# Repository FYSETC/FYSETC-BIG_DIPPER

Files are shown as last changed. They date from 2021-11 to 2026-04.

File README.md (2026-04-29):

# Big dipper

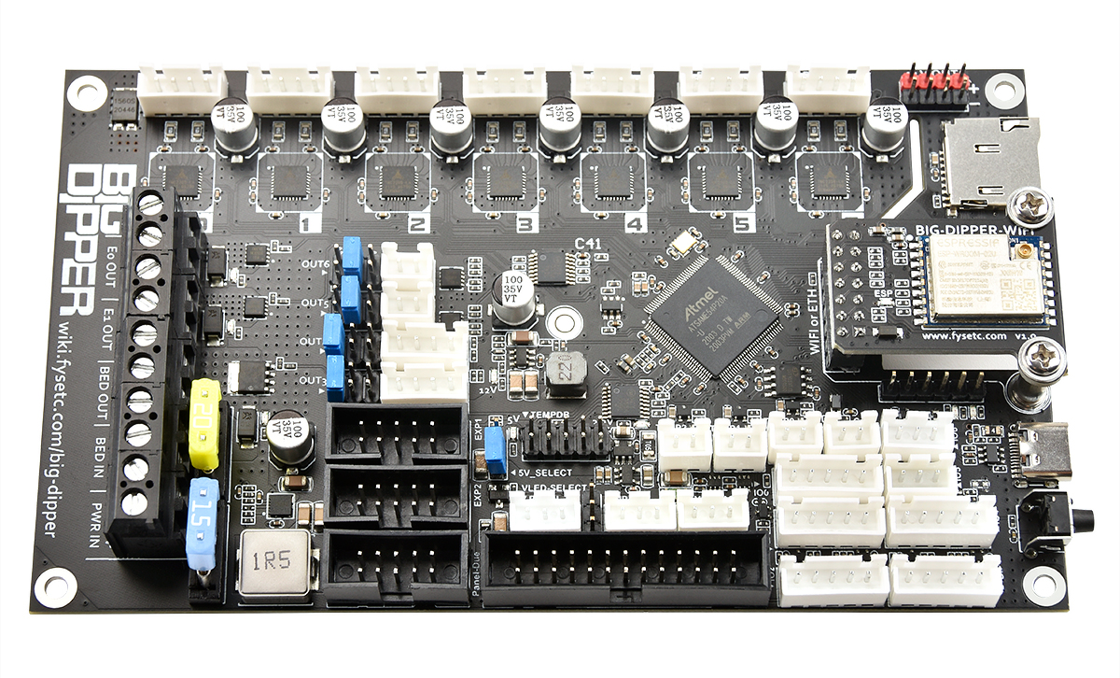
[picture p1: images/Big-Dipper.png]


## 1. Introduction

FYSETC BIG DIPPER motherboard, reprap firmware(RRF), 32bit 3d pirnter motherboard base on DUET3 mini5+ and mini2+. Based on the good ecology of the RRF firmware and on-board 7-axis (7xTMC2209), the board can be easily configured in a variety of 3D printer models, such as VORON series, Annex Engineering K3, multi-Z-axis models, double-X models etc.

### 1.1 Featrues

1. Compact size: 148.5 x 87mm

2. Base on SAME54P20(ARM Cortex M4 @120Mhz)， fully compatible with Duet3 Mini5+

3. Onboard 7 TMC2209 stepper motor drivers

4. Input and output IO full TVS protection

5. 28V maximum input, 12V@2A DC-DC (12V fan power supply), 5V@8A DC-DC (power supply for Raspberry Pi  and the system), two 3.3V@0.6A LDO (power supply for MCU and 3.3V peripherals respectively)

6. Two car fuses for hot bed input and main power input

7. Using XH2.54 connector, each interface function is exactly the same as mini5+

8. 7x PWM power MOSFET output（ 1 for heatbed, 2 for hot end, 4 for fans ）

9. RepRap Discount Smart Controller compatible sockets ，EXP1 and EXP2。Support monochrome displays such as 2004 ，12864。

10. UART1-Raspberry Pi pin header (including 5V@5A power supply)

11. Onboard TF card slot

12. Type-C USB socket

13. 3 Thermistor/PT1000 inputs and support for 2 PT100 or thermocouple inputs via the optional daughterboards.

14. Both Wifi and Ethernet versions

16. CAN bus that supports the next generation of Duet3D expansion boards, smart tools and 
      custom addons.
    
16. Set up your printer and update the firmware through the web interface.

17. All common 3D printer geometries are supported

18.  Support for a wide range of Z probes including DC42’s IR Z probe and the Duet3D Smart Effector for delta printers.

## 2. Firmware

The motherboard is developed on the basis of the due3mini5+ motherboard, and the firmware is compatible. 

Firmware Configuring:

https://docs.duet3d.com/en/How_to_guides/Configuring_firmware

duet3mini5+ firmware:

https://github.com/Duet3D/RepRapFirmware/releases

- Compatible RepRapFirmware versions: RRF 3.2 and later

For firmware update instructions, see [Installing and updating firmware](https://docs.duet3d.com/User_manual/RepRapFirmware/Updating_firmware).

If running from an SBC, see [SBC setup for Duet 3](https://docs.duet3d.com/User_manual/Machine_configuration/SBC_setup).

### 2.1 Steps to use RRF

- **Step 1: Power supply**

  The motherboard needs to provide a 24V power supply, and the jumper cap in the 5V_SELECT position is required to select 5V&DCV

  

- **Step 2: Update firmware**

  The firmware of the motherboard may not be the latest when it leaves the factory. You can use USB to upgrade the firmware, download the latest firmware, connect to the computer via USB, and quickly press the motherboard reset button twice, then a new disk will appear on the computer. Just copy the firmware

- **Step 3: config**

  There is a `config` folder in the `Firmware` folder next to this readme file, which is just a sample configuration for running RRF. Copy all the contents of the config folder to the root directory of sdCard, and insert the sdCard into the card slot of the big-dipper motherboard.

## 3. Hardware

If you want to build a machine with RRF firmware on the big-dipper motherboard, then you can use four ways to communicate/control with big-dipper. They are USB serial, mini12864, Panel-due and Ethernet/WIFI Module. And you can get sch files on Hardware folder next to this README.

**Wiring diagram**

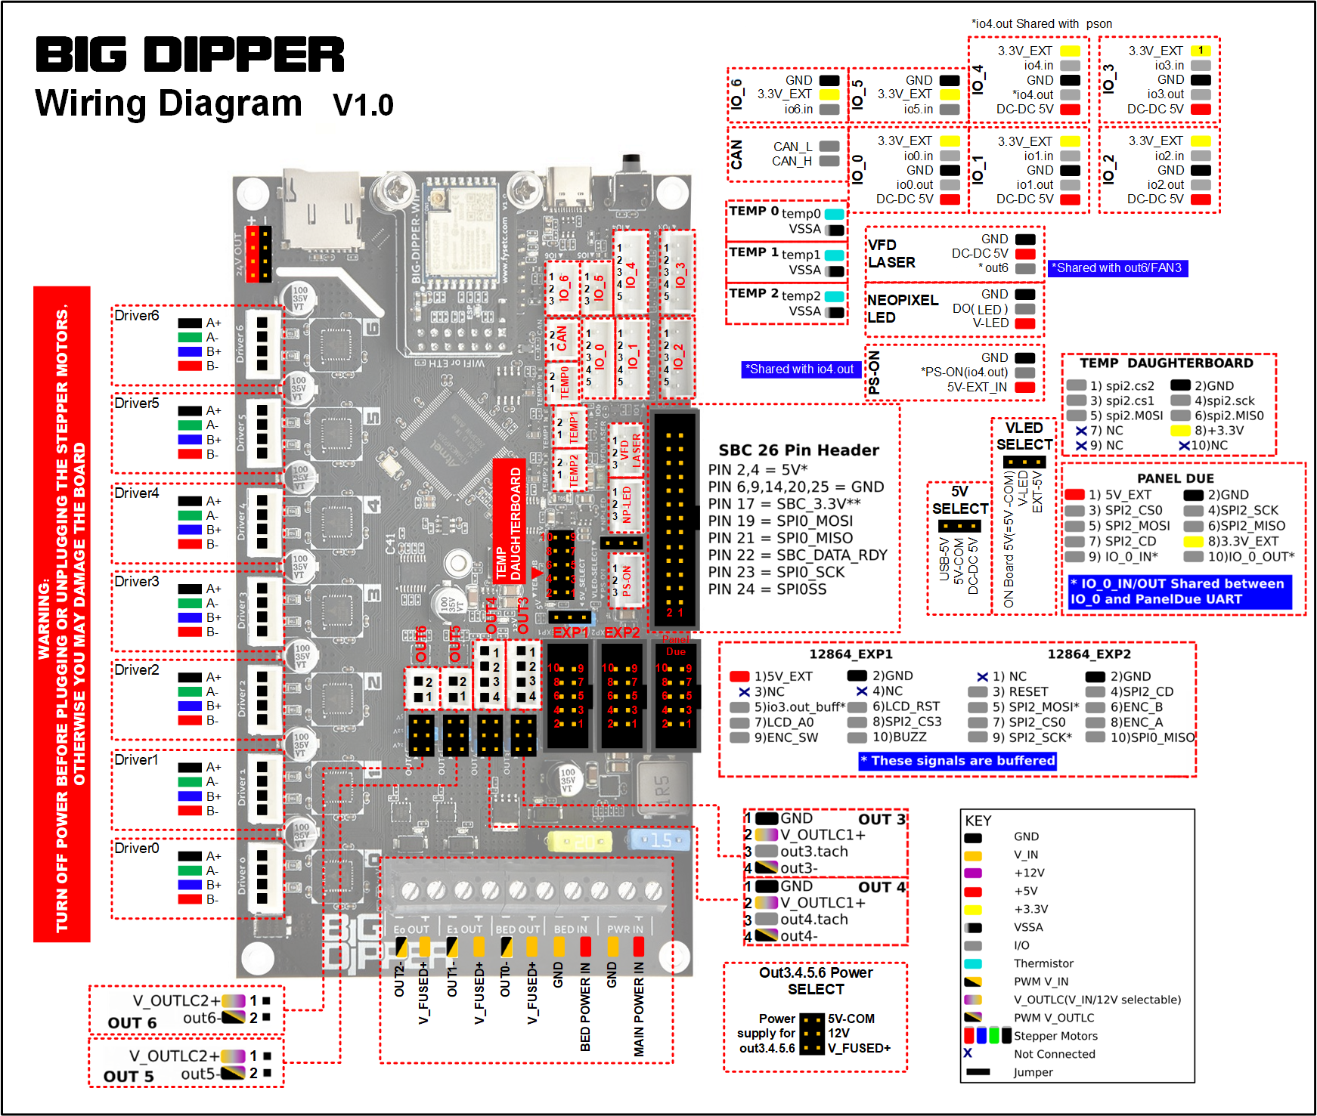
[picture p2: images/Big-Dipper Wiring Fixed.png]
Big-Dipper Wiring


### 3.1 USB serial

After the motherboard is correctly connected to the power supply, insert the SDcard and the sample configuration (you are recommended to configure it yourself), and then use the USB data cable to connect to the computer, you can use RRF Gcode to control the motherboard.

### 3.2 FYSETC mini12864

This is a low-cost external display/control solution. You can use FYSETC mini12864 by adding the following code to the config.g file (the sample configuration has been added)

```
M918 P2 E2 F2000000 C40 R6			; enable ST7567-based 12864 display
M150 X2 R255 U255 B255 S3			; set all 3 LEDs to white
```

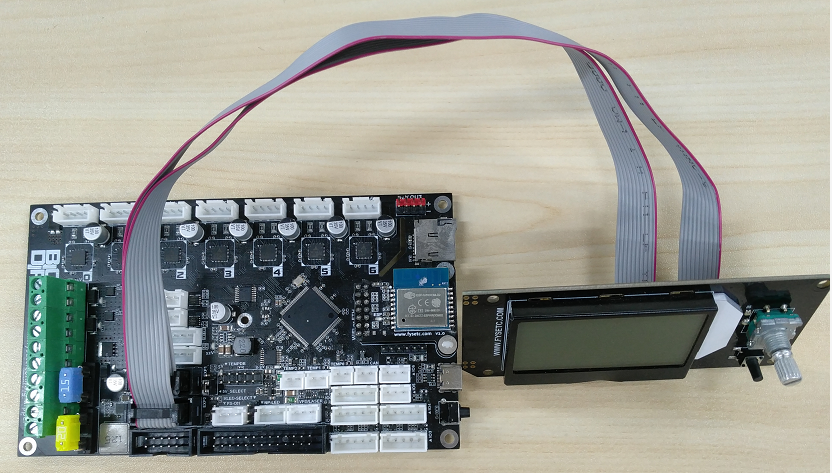
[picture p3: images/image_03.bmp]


### 3.3 Panel-due

Compared to mini12864 using a rotary encoder to control the motherboard, it is more convenient to use Panel-due with touch control. You only need to add the following code to the config.g configuration file (the sample configuration has been added)

There are two ways to connect the screen to the motherboard:

1. Use XH2.54 interface to connect, pay attention to the need to adjust the line sequence

2. Use 2x5 cable connection

```
M575 P1 S1 B57600                   ; enable support for PanelDue
```

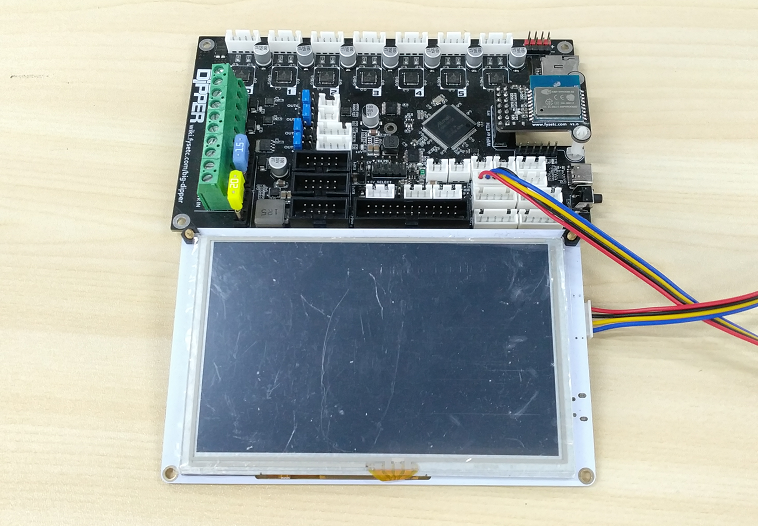
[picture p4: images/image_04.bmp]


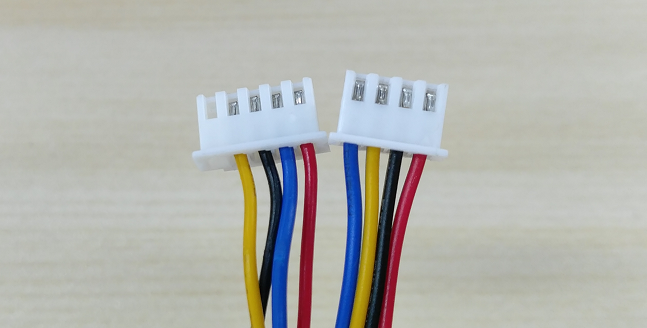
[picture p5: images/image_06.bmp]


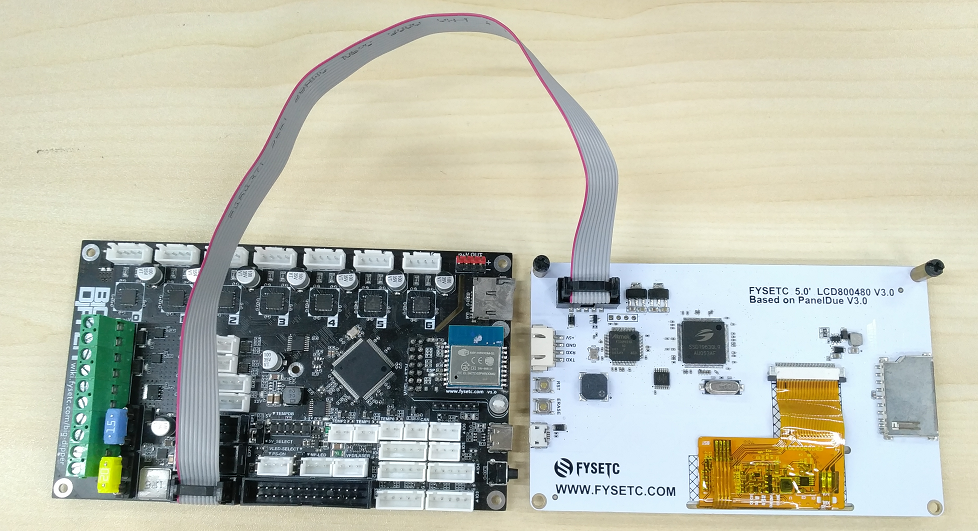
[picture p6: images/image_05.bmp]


### 3.4 Ethernet/WIFI Module

#### 3.4.1 Ethernet Module

If you use the Ethernet module, you need to add the following code in config.g (NO need for wifi module).

```
M552 P0.0.0.0 S1    ; enable network and acquire dynamic address via DHCP
```

After connecting to the Ethernet, the panel-due screen or serial port will output the IP address (192.168.x.xxx), and you can open the Duet Web Control in the computer web page WITH this IP address.

#### 3.4.2 WIFI Module

If you use the wifi module, you need to manually configure the SSID and PASSWORRD (you can use the serial port to send instructions)

1. Stop wifi module

   ```
   M552 s-1
   ```

   You should receive `WiFi module stopped`.

2. Start wifi module

   ```
   M552 s0
   ```

   You should receive `WiFi module started`.

3. Setup your wifi network SSID and password.

   ```
   M587 S"ssid" P"password"
   ```

   The module should connect to your wifi network in 30s.

## 4. Other features

### Driver 0~6

```
M569 P0.0 S0       ; physical drive 0.0 goes forwards
M569 P0.1 S0       ; physical drive 0.1 goes forwards
M569 P0.2 S0       ; physical drive 0.1 goes forwards
M569 P0.3 S0       ; physical drive 0.2 goes forwards
M569 P0.4 S0       ; physical drive 0.3 goes forwards
M569 P0.5 S0       ; physical drive 0.4 goes forwards
M569 P0.6 S0       ; physical drive 0.5 goes forwards
```

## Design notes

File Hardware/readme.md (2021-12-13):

In this folder you will find drawings and CAD data for the Big Dipper.

# Fusion360 Data for Big Dipper v1.1
This data Based on measurements and the PCB layout from this folder.

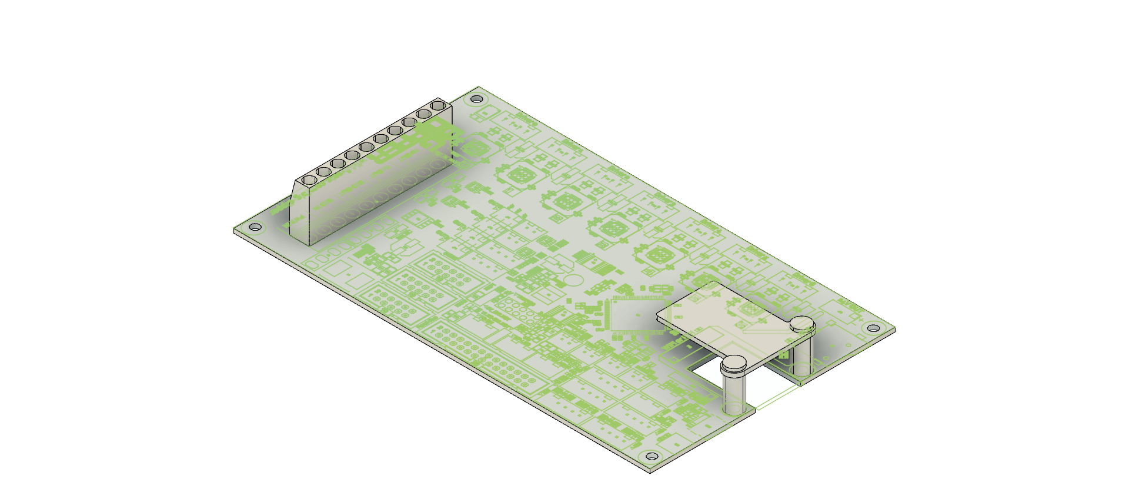
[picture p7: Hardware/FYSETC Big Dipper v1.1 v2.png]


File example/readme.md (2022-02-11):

Please find here several example projects on how to use the BigDipper 3D printer controller board.

* Build or modify your Independent Dual Extruder (IDEX) printer and make use of all the Stepper drivers and connections that BigDipper have.

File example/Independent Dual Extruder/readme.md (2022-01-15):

# Using the Fysetc Big Dipper to build an IDEX 3D printer with RepRap Firmware printer

## Wire Diagram
This is how I wired the IDEX printer with his two extruders, dual axis and all endstops.
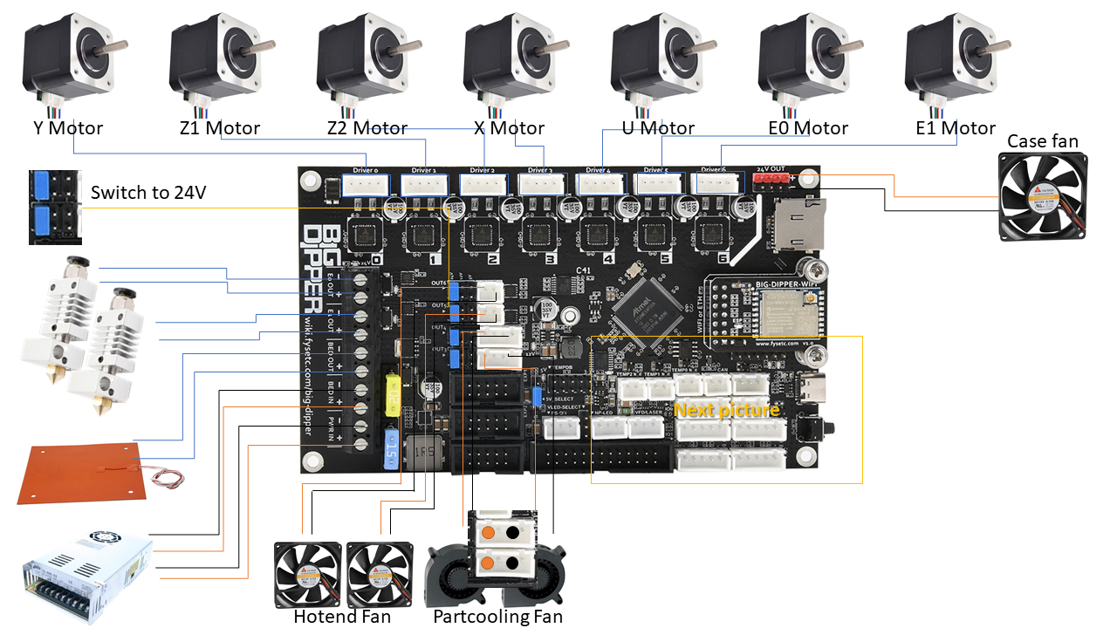
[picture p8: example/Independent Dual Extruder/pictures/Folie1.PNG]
Pinning 1

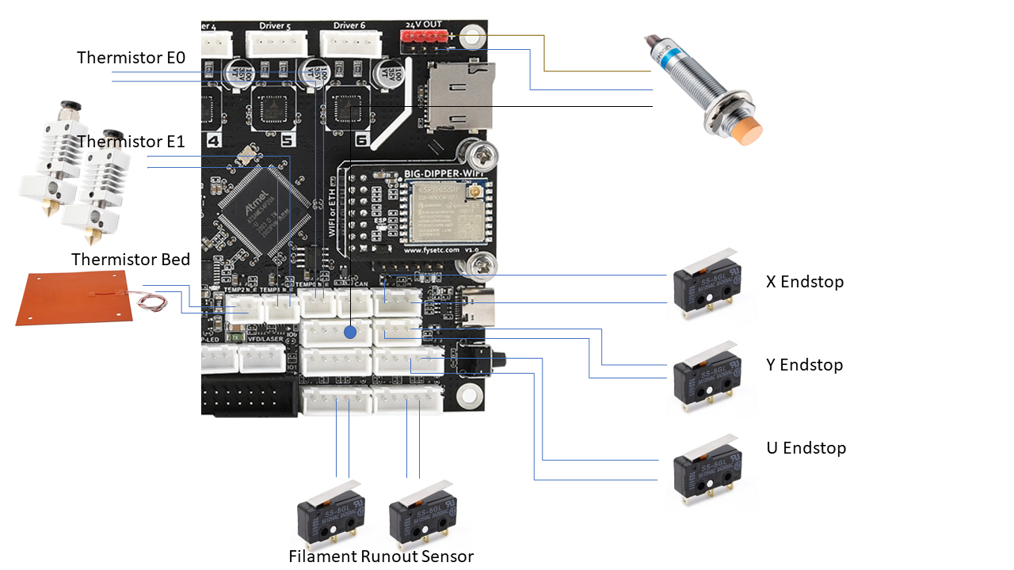
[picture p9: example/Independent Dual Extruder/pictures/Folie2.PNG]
Pinning 2


If it is not clear to see, I also did some pictures.
For the Y and both Z Motors, I used the exising cables. For both E and X I bought new cables with 1m length.

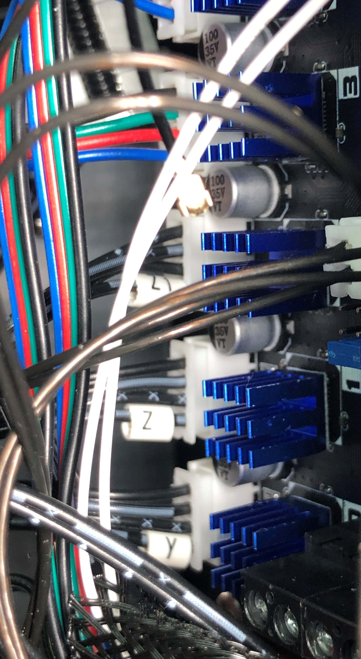
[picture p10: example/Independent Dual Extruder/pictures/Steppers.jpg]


For the Fans on the Hotend you need to set the Jumpers to 24V. See the pinning on the picture.

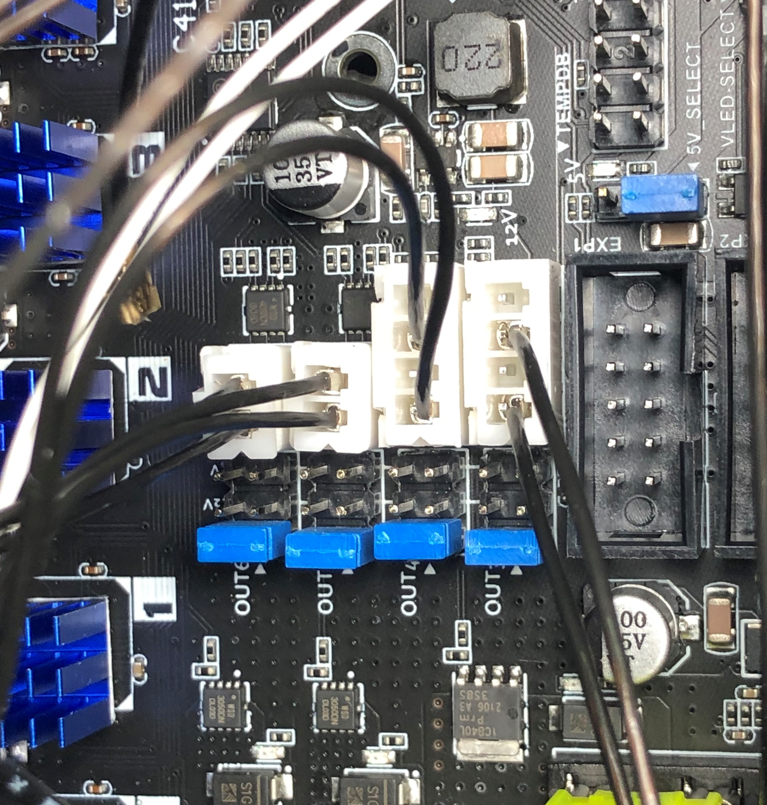
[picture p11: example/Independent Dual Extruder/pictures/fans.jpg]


Also for the Endstops and the proximity sensor the Pinning is very impotant. There is no polarity but you have to take the right PINs in the JST-XH connectors.

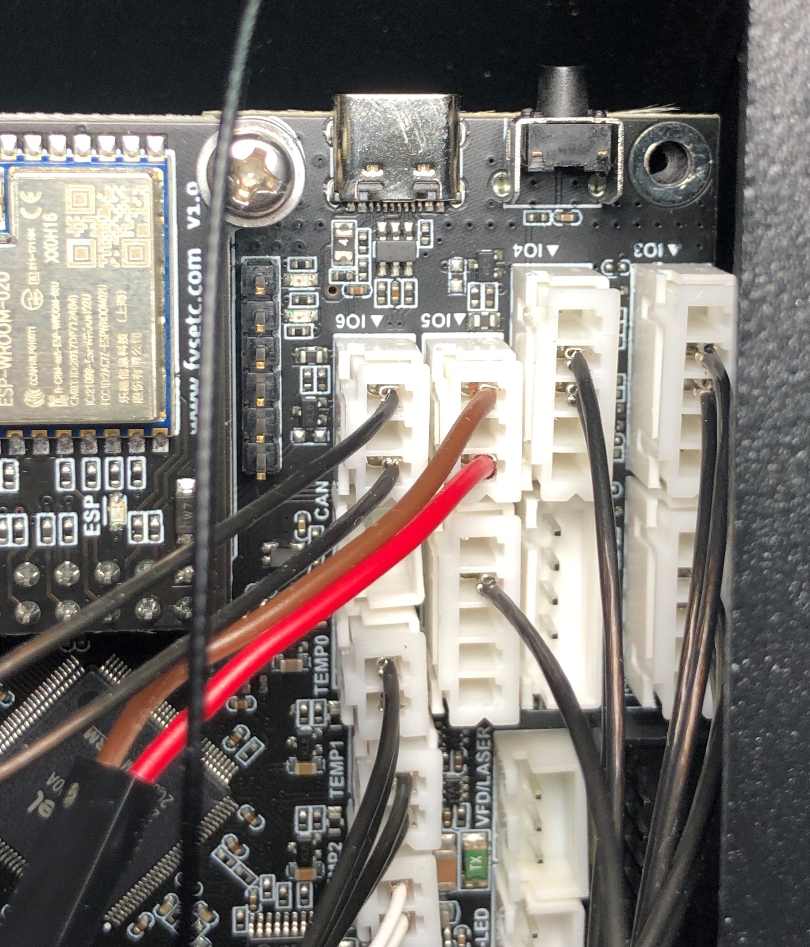
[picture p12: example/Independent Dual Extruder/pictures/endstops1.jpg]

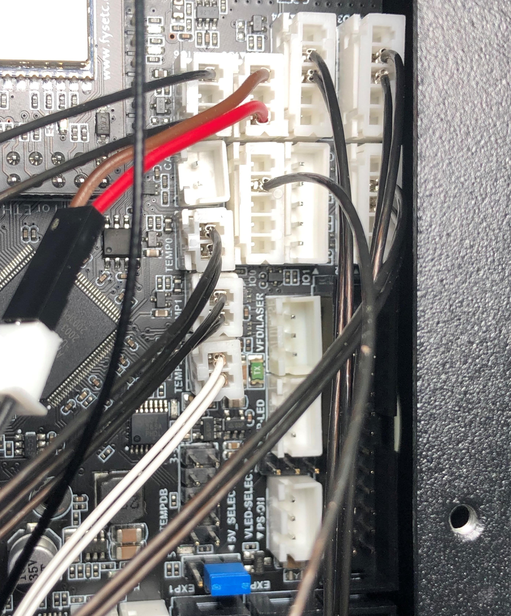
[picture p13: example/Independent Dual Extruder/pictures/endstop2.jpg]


For the Probe I needed for this project also +24V and for the Casefan there was no additional Fan Plug free. So both went to 24V.
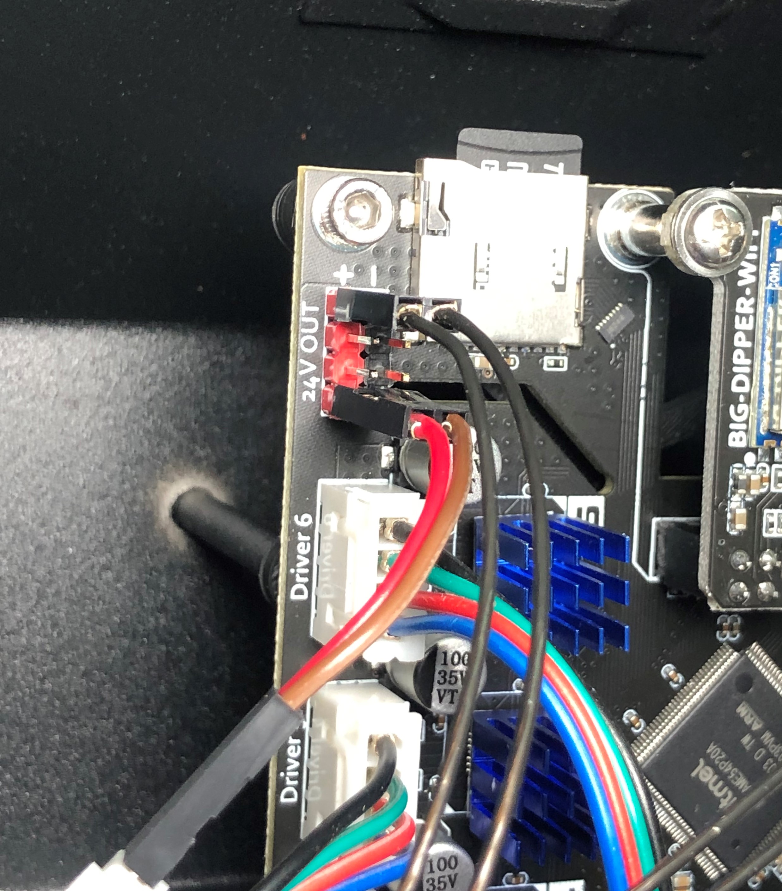
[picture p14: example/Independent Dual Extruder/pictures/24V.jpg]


| Function | PIN | comment |
| --- | --- | --- |
| Y Axis Motor | Driver 0 | |
| Z1 Axis Motor | Driver 1 | |
| Z2 Axis Motor | Driver 2 | |
| X Axis Motor | Driver 3 | left Printhead |
| U Axis Motor | Driver 4 | right Printhead |
| E0 Axis Motor | Driver 5 | left Extruder |
| E1 Axis Motor | Driver 6 | right Extruder |
| PSU 24V | Pwr in | |
| PSU 24V | Bed in | |
| Heated Bed | Bed out | |
| Hotend E0 | E0 out | left Printhead |
| Hotend E1 | E1 Out | right  Printhead |
| X-Endstop | io6.in | see pic for PIN |
| U-Endstop | io4.in | see pic for PIN |
| Y-Endstop | io5.in | see pic for PIN |
| Z-Probe | io0.in | only for Signal, see pic for PIN |
| Bed Thermistor | out0 |  |
| E0  Thermistor | out1 |  |
| E1  Thermistor | out2 |  |
| Case fan | 24V out |  |
| Z-Probe | 24V out |  |

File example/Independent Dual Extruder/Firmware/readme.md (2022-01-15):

For the use in this example on an IDEX 3D printer, the Firmware also need to have a lot of differences compared to a single extruder setup.
Please find here the Firmware Settings based on *RepRapFirmware for Duet 3 Mini 5+ 3.4.0beta7 (2021-12-16)*.

> Not just the config.g is changed. Also the Tool change files.

You also need the correct Slicer Setting to let it work. Please check as well the Prusa Config.

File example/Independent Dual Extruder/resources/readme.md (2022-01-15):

Each printer is a little different. You can carry over most of the setting. But some you need to tune for your printer.
Here is a link list of resources that you should visit to avoid the printer crashing into the bed for example.

- First you need to tell the board about your WiFi.  
I did that with Pronterface and this steps: https://duet3d.dozuki.com/Guide/1.)+Getting+Connected+to+your+Duet/7  
Tipp: If you add ' before a letter, also Pronterface allowes small Letters. P'A'S'S'W'O'R'D = Password
- Test and calibrate a Z probe https://duet3d.dozuki.com/Wiki/Test_and_calibrate_the_Z_probe#Section_Calibrate_the_Z_probe_trigger_height
- Calibrate IDEX https://duet3d.dozuki.com/Wiki/ConfiguringMultipleIndependentXcarriagesCartesian#Section_Calibration

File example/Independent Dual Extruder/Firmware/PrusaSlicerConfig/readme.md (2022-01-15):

Slicer Profiles for the RRF IDEX 3D Printer build.

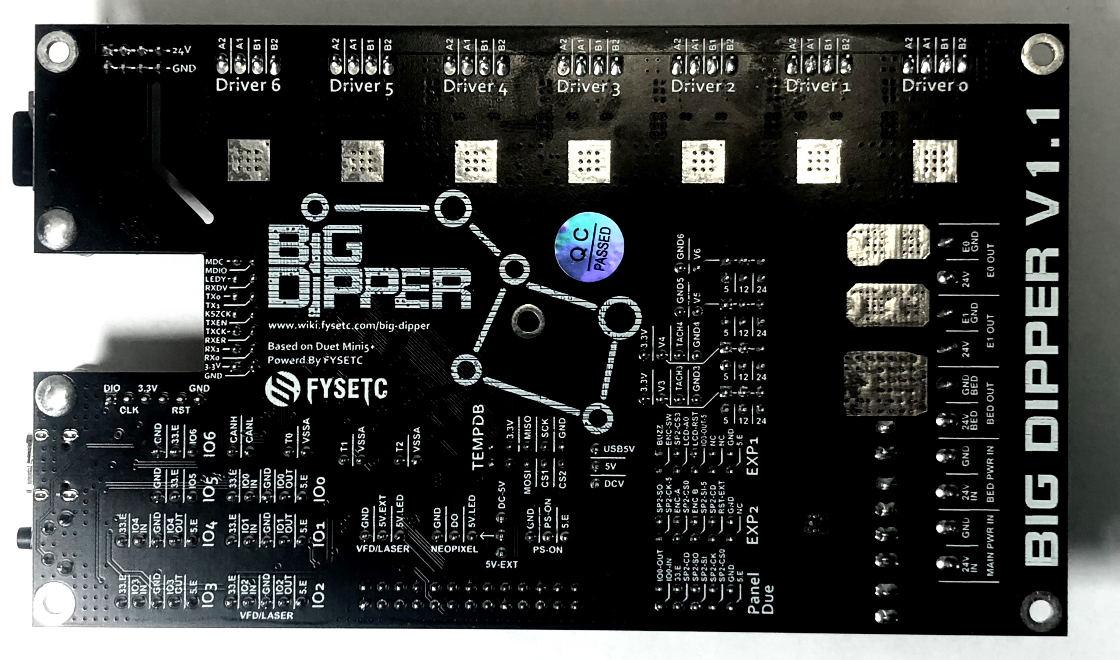
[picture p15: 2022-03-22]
images/BigDipper_back.jpg

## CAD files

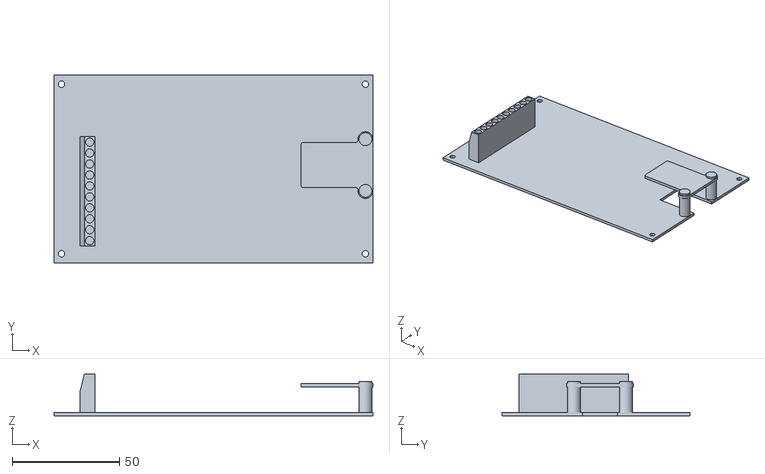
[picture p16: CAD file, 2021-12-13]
Hardware/FYSETC Big Dipper v1.1.stl
148.6 x 87.5 x 19.5

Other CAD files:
Hardware/BIG-DIPPER V1.1.dwg

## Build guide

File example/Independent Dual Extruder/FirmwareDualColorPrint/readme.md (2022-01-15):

This files are for Dual Color prints where both toolheads work on the same object.

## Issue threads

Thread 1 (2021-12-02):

PCB drawing mounting holes

moth4017, 2021-12-02:
Hi does anyone have the dimensions of the mounting holes?

the0bone, 2021-12-02:
M3

See my CAD data https://github.com/the0bone/FYSETC-BIG_DIPPER/tree/main/CAD

moth4017, 2021-12-02:
Thank you

________________________________
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

Closed 2021-12-16.

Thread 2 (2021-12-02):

Allow Branch

the0bone, 2021-12-02:
While I can not create a branch from the Big Dipper, I created a Fork to include my CAD data.
https://github.com/the0bone/FYSETC-BIG_DIPPER/tree/main/CAD

GerogeFu, 2021-12-10:
Do you mind if i copy them to our github?

the0bone, 2021-12-10:
>

Sure you can.
But if you add me as contributor to the project, I can open a branch instead of a fork and have the data there and you can commit them to the main branch (yours) if you want. Thats the way how github is working and thats way more efficient.
Also because I'm adding more content while I rebuild my IDEX printer with that board now.
So also a PIN out plan will be there shortly.

GerogeFu, 2021-12-11:
You have write access to the repo now.

Closed 2021-12-11.

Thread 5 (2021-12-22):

Stepper motor very noisy

Quasar973, 2021-12-22:
I'm be installing a big dipper on a mingda d2, i've connected 9nly one stepper motor for testing movements but the motor is veru loudy.
firmware version 3.4.0beta 5

jero64, 2022-02-04:
im replacing a duet 2 wifi with this board because the TMC2209 driver is more silent than the TMC 2660 and hopefully gives so less vibration on my hotend.  I got the machine moving but i ran into other issues, listed new here.

darthscsi, 2022-03-09:
I second issue.  Steppers give out a distinct hissing sound.

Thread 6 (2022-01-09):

Schematic issues

moth4017, 2022-01-09:
Hi please can you check the schematic is correct

X2G- missing of schematic
X2H -missing of schematic

OUT3 AND OUT4  Pin order not the same on Schematic as PCB

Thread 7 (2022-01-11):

Board does not respond anymore

chehoff, 2022-01-11:
On a new board don't connect to PC. Clip set to 5V. 5v red led light on, 3.3 red led light on, but status red led light on 1sec per 15 seconds. Does not create COM-port on pc, does not respond to the inserted sd card with firmware. When press the motherboard reset button twice, new disk appearing on the computer, but only 2-3 second, then board rebooting. This may be due to a bad bootloader, but I don't find information about replace it.

phillc54, 2024-01-03:
Hmm, one year later and I have exactly the same issue.

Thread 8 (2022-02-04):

PT1000 sensor doesnt work

jero64, 2022-02-04:
For my Hotend i got a PT1000 thermistor, with the usual config the temp reading is way to high like 361 degr C.
M308 S1 P"temp1" Y"pt1000" T100000 B3950 R4700					     ; configure sensor 1 as thermistor on pin temp1
M950 H1 C"out1" T1											     ; create nozzle heater output on e0heat and map it to sensor 1
M307 H1 B0 R2.260 C374.9 D3.97 S1.00 V25.0						     ; disable bang-bang mode for heater  and set PWM limit

jero64, 2022-02-09:
The standard config doesnt work. you have to add or alter thr R value to 2200 in the config file which is the value of the resistors on the board.
Thats seems to de the job.

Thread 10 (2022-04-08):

Missing Documentary

SvenBarracuda, 2022-04-08:
Cant find any description of the Connectors and Jumper brigdes.
Try and error could be expensive

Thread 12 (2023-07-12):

SBC mode not working

hbiedka, 2023-07-12:
I have just bought Big Dipper board and I'm going to run it with Raspberry Pi i n SBC mode.

First of all, I replaced firmware for Duet5Mini+ suitable one, downloaded from Duet3d website. In no-SBC mode it was working fine.

For now I have tried to connect RPi using ribbon cable out of the box. And the Raspberry Pi does not recognize the board. After connecting to RPi's IP DWC throws an error "Timeout waiting for transfer ready pin", which I met when connection between original Duet and RPi is disconnected.
To double-check all connections I connected original DuetMini5+ board and everything works fine.

At the moment I have checked that there is no signal on RDY pin (GPIO 22), so the communication by SPI is not starting up.
After that, I suspect there is something wrong with the board.
SD card slot on Big Dipper board is empty. I am using Duet-provided RPi card image.

I am not sure is there any jumper or MCU configuration causing it is not working out-of-the-box. I have checked Big Dipper schematics and I figured out there is only a buffer (supplied from 3.3 V got from RPi) between MCU out and GPIO port.

I have also tried to find out some similar issues but I figured out that SBC mode in FYSETC boards is not quite common.

Has somebody met similar problems?

Dmitry-kalinin, 2024-09-23:
Have you been able to resolve this issue? I’m having it as well

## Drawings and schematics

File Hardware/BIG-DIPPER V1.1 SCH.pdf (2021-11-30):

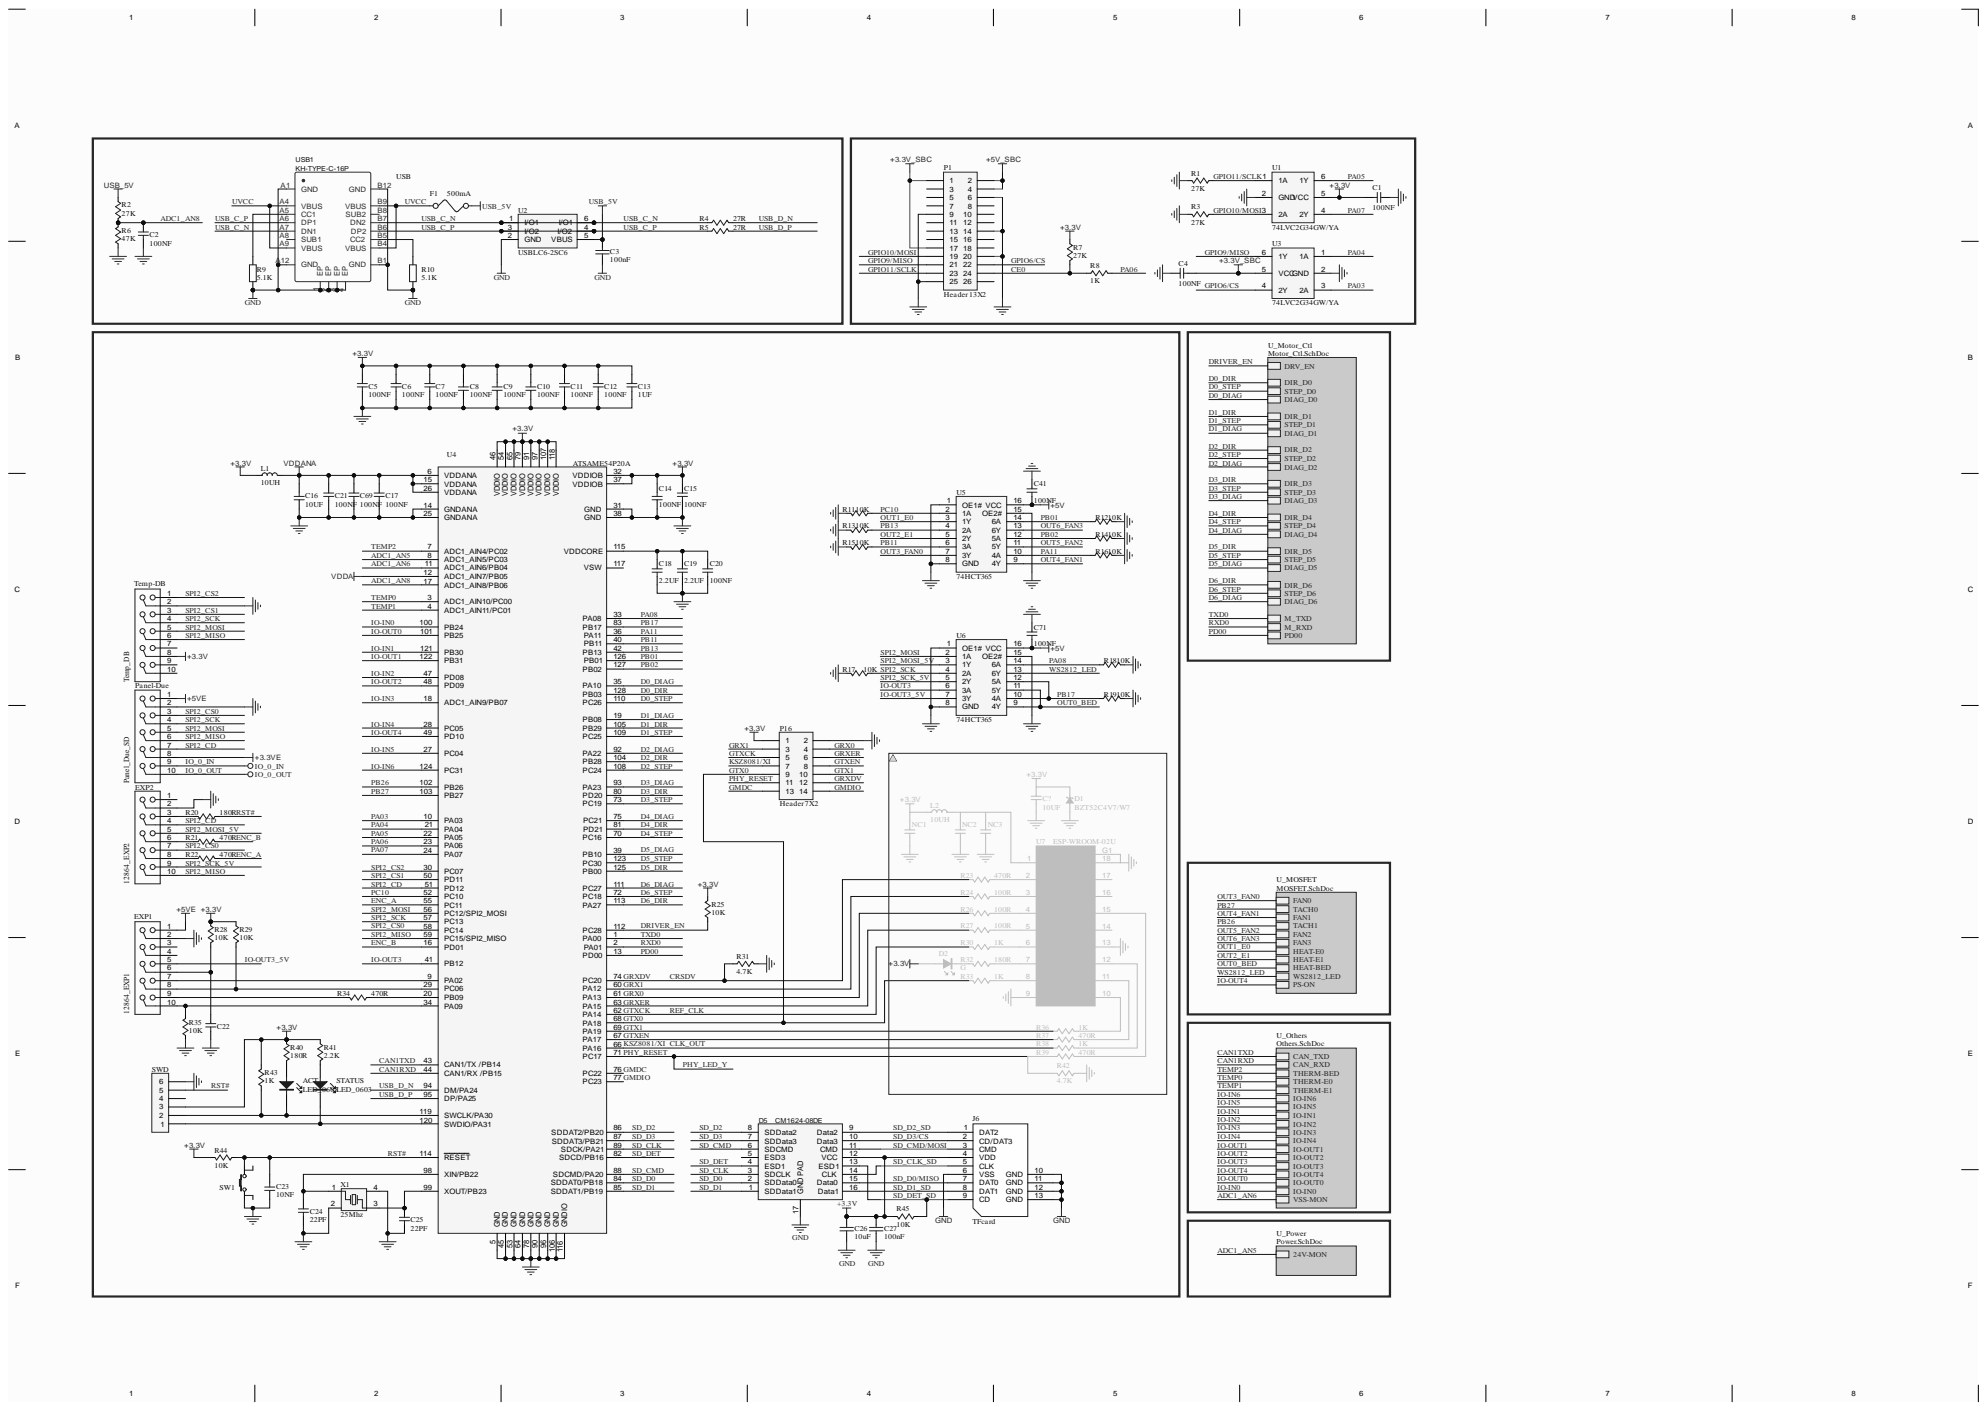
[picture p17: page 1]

8 | | | | | GRX1

9 | R34 470R | | PA09 34 PB09 20 PC06 29 | | GRX0

10 | | | | | GRXER

R35 10K | C22 +3.3V | CAN1/TX /PB14 43 | | GTXCK REF_CLK | | R36 | 1K

GTX0

GTXEN | R37 | 470R
KSZ8081/XI CLK_OUT | R38 | 1K

SD_DET_SD

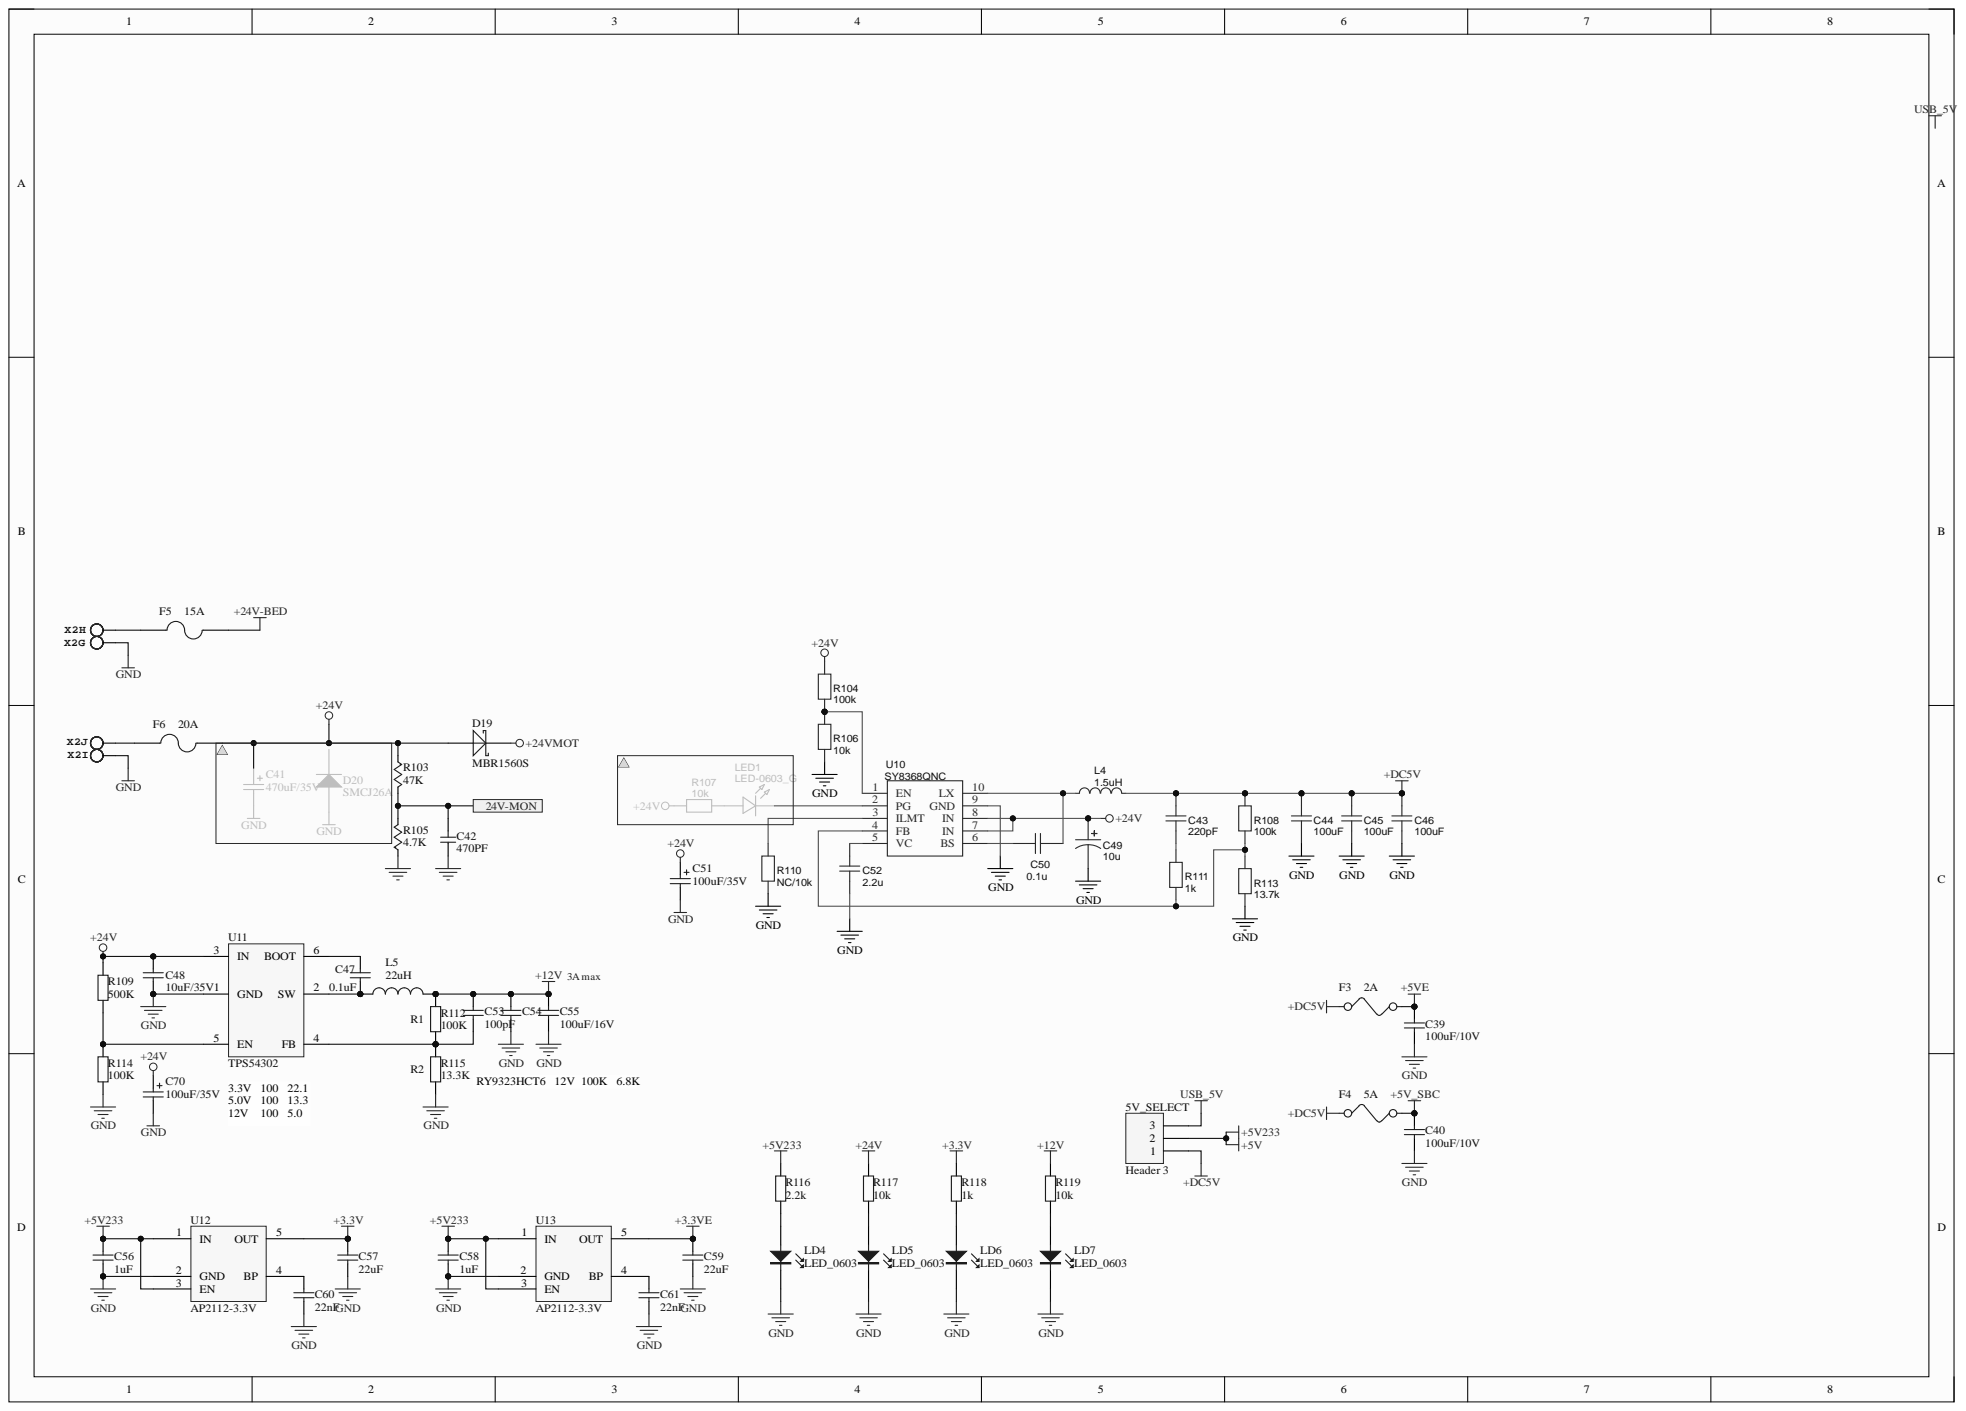
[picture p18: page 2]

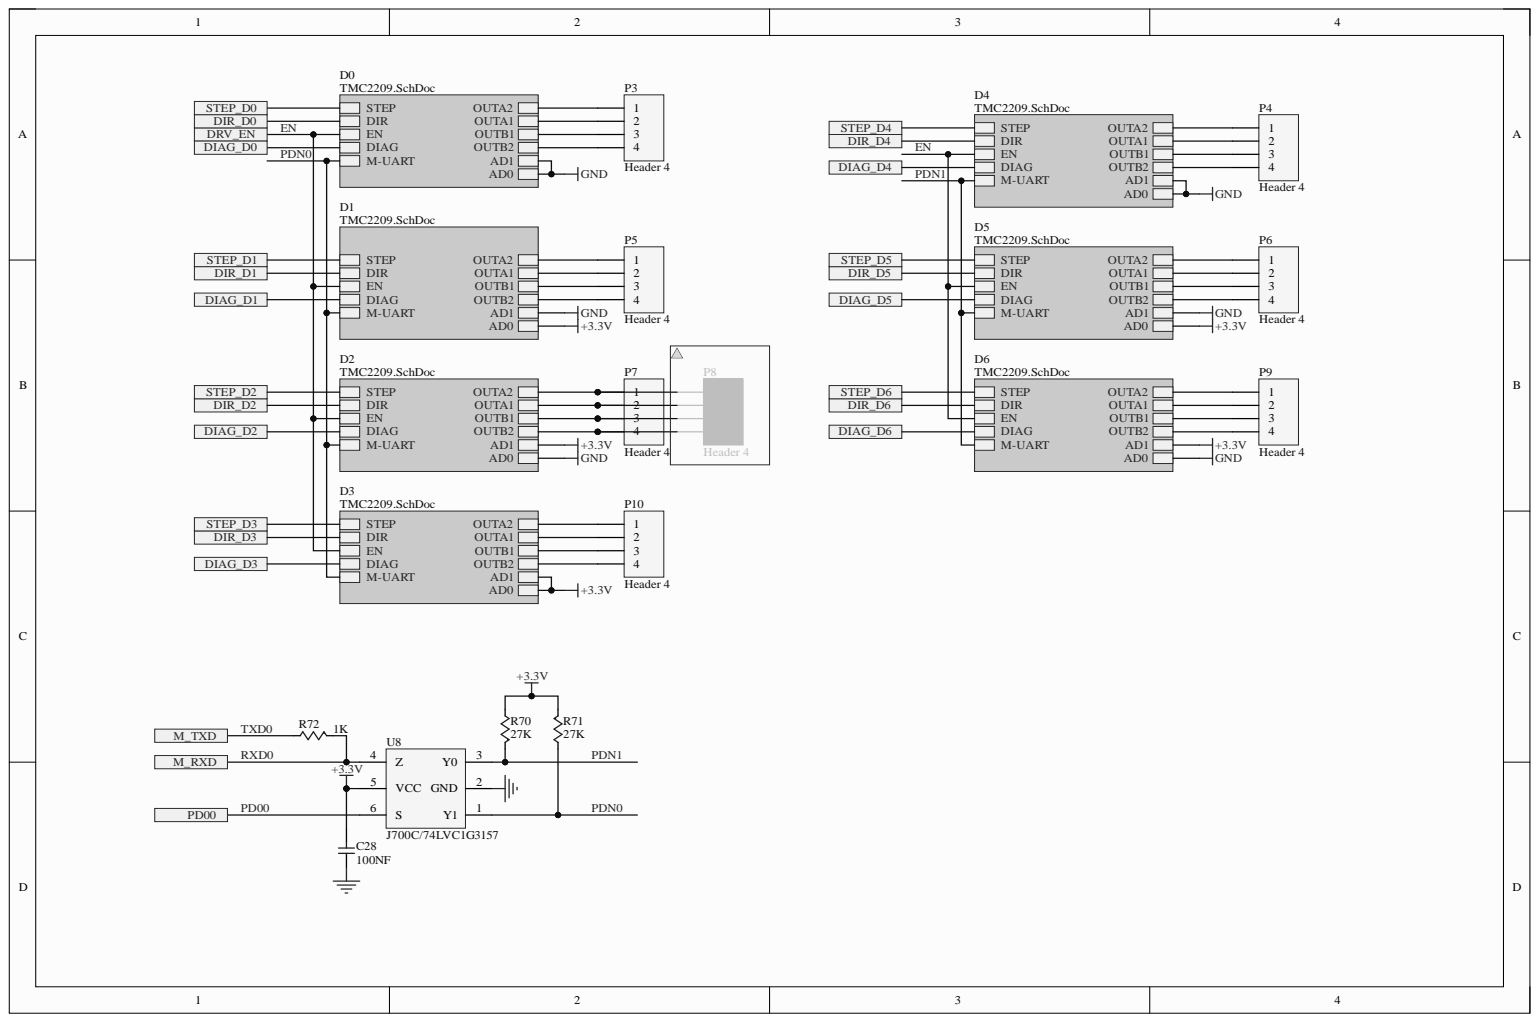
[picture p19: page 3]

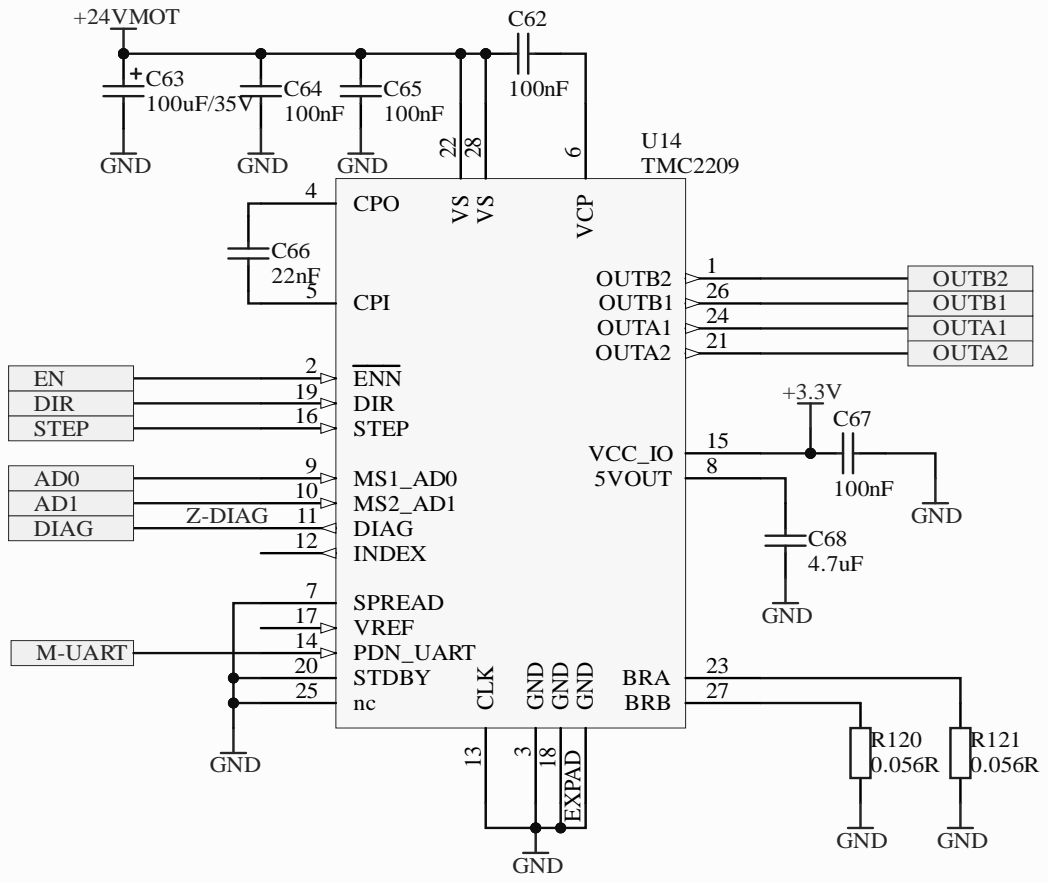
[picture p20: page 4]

VREF 17

STDBY 20

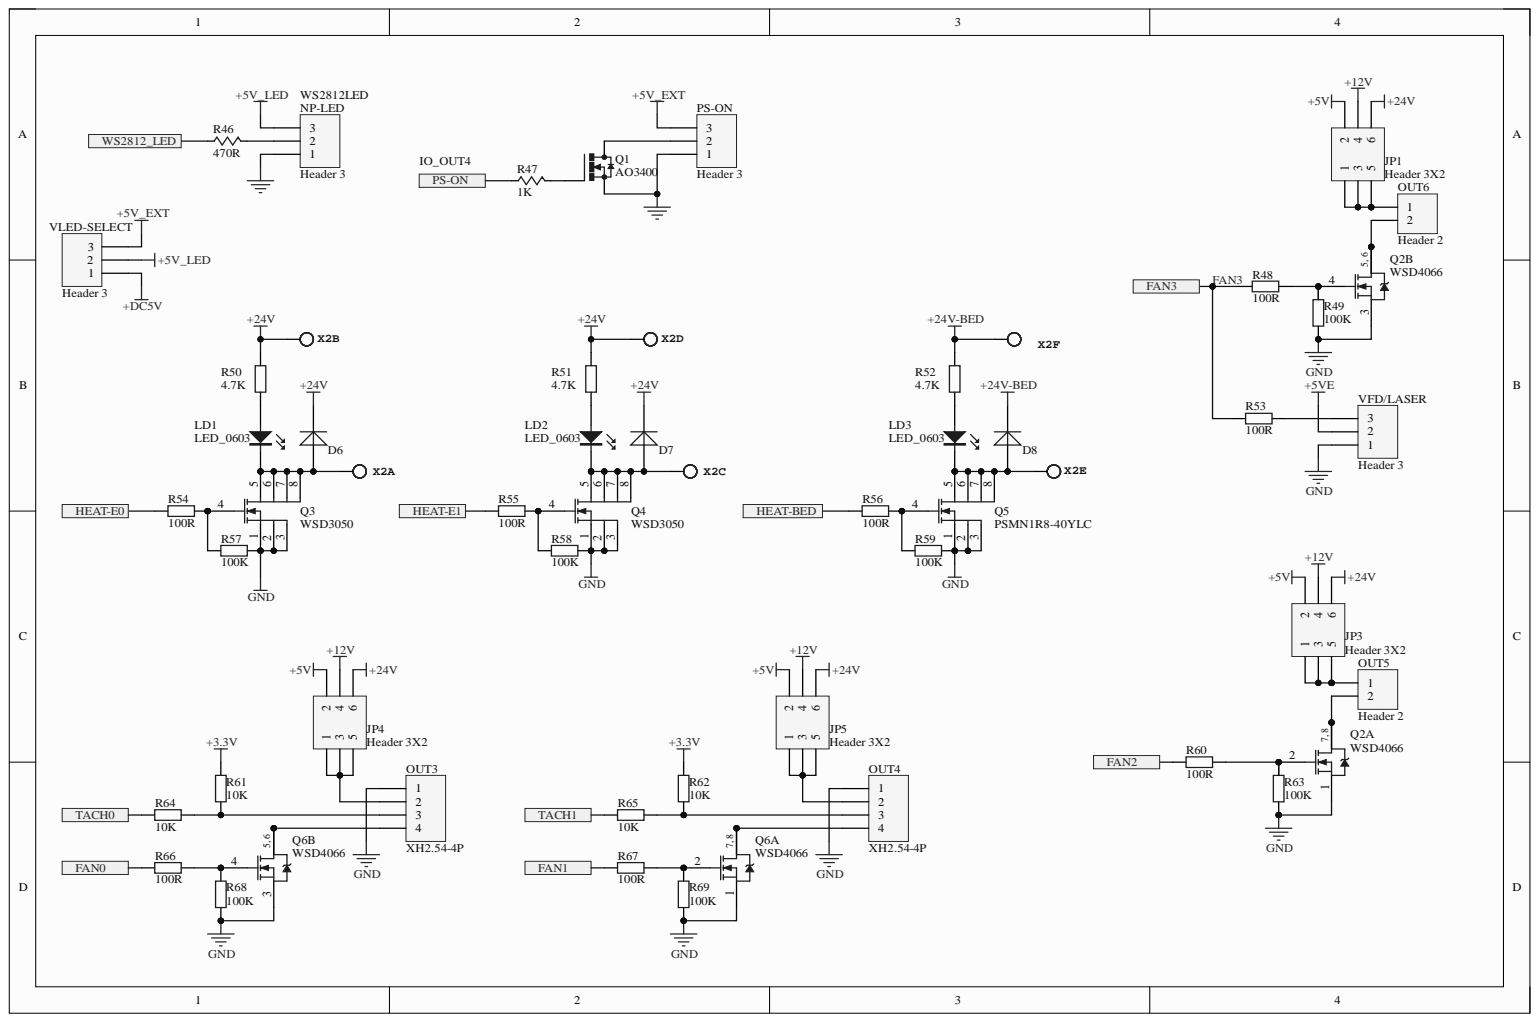
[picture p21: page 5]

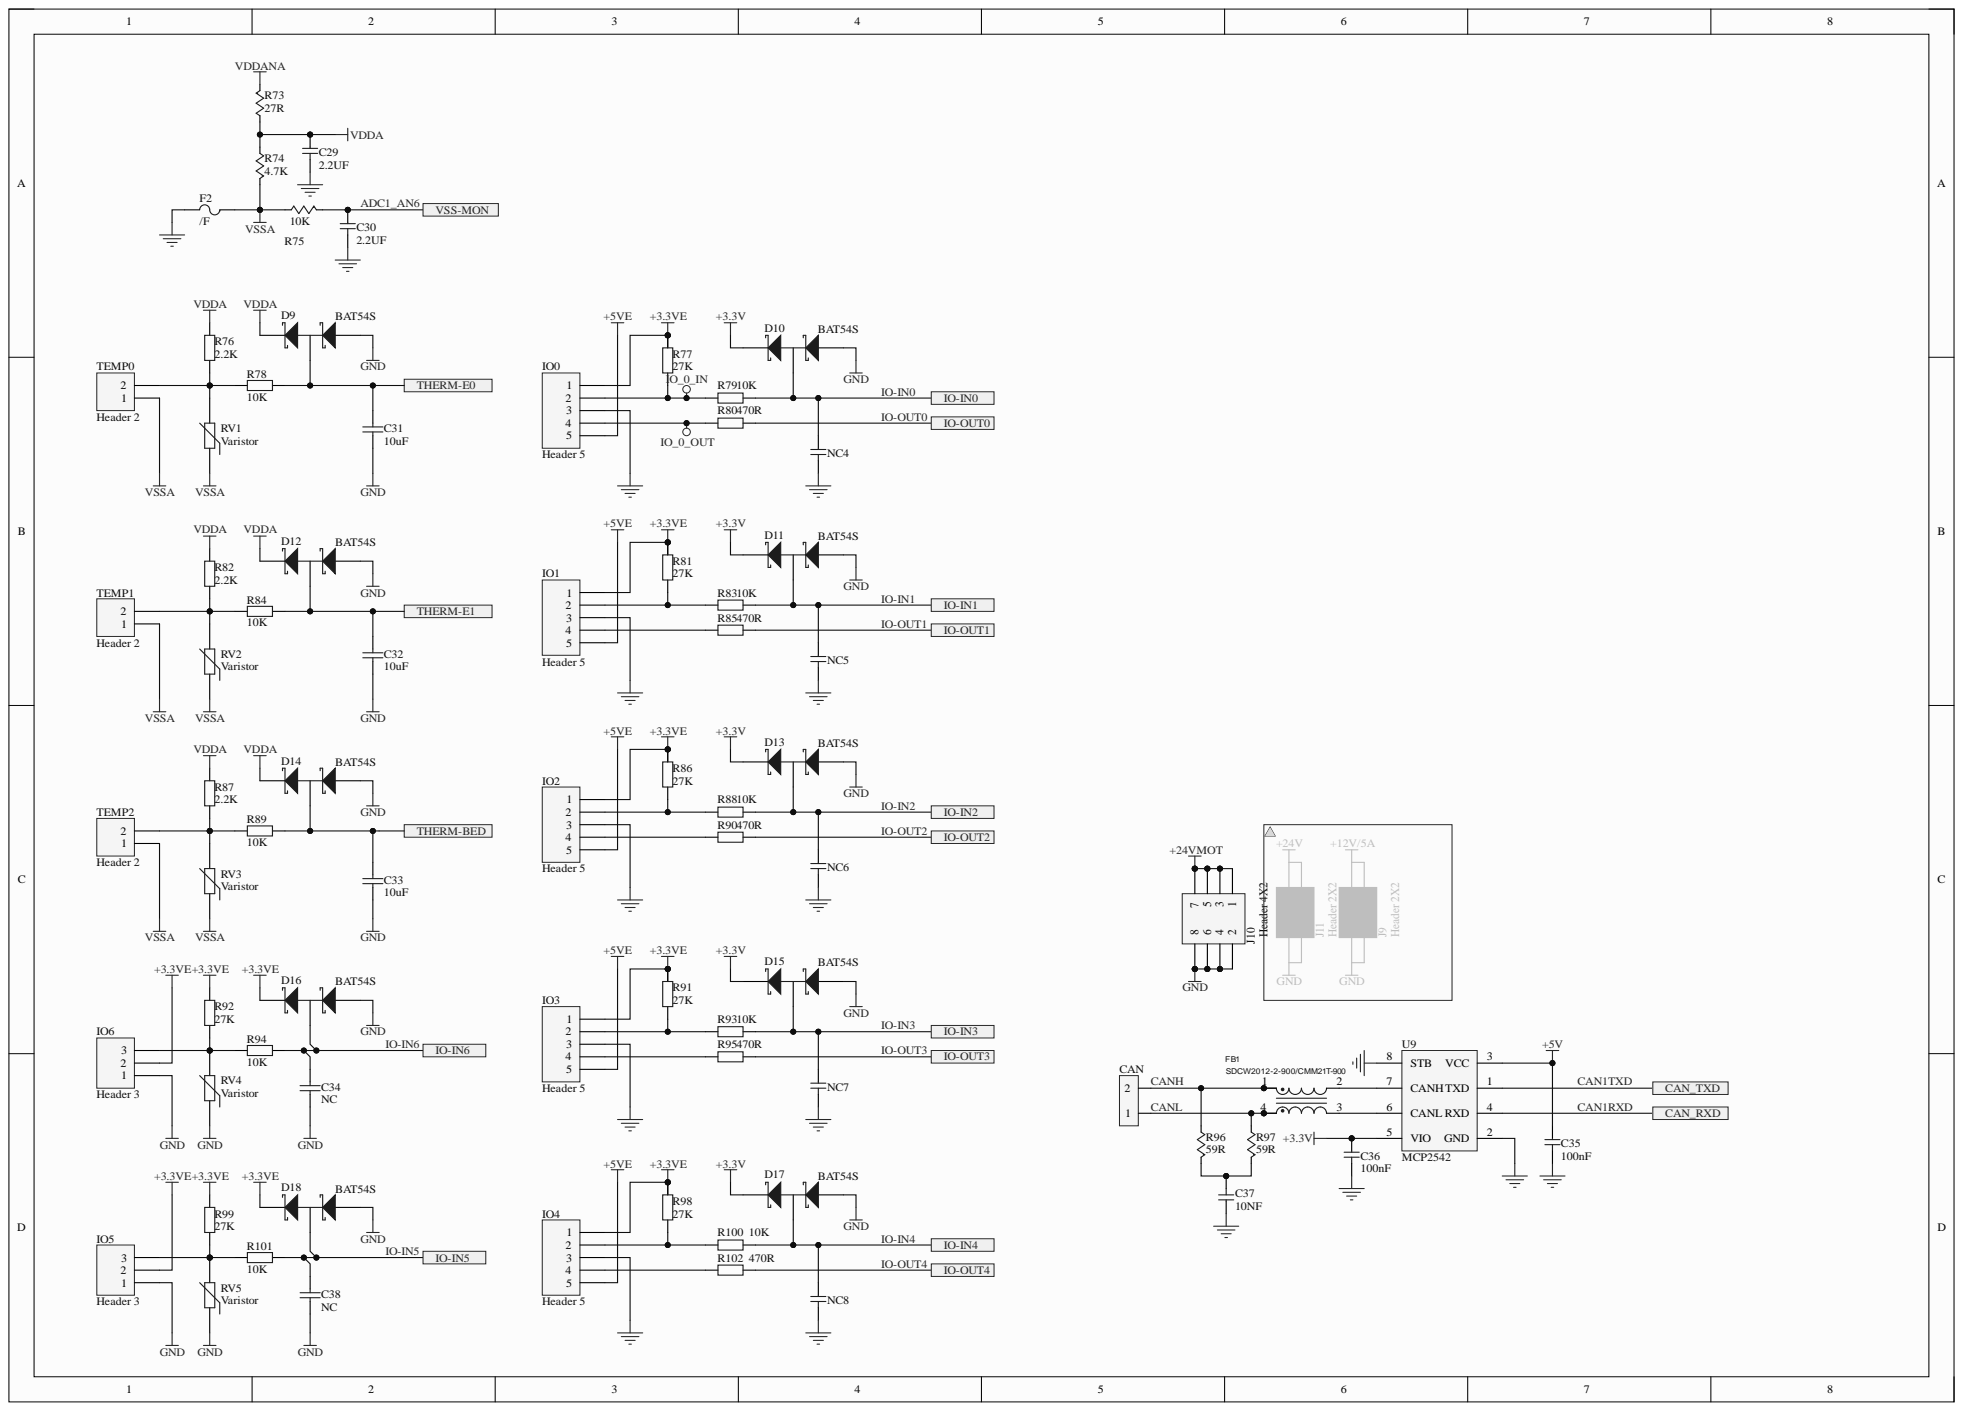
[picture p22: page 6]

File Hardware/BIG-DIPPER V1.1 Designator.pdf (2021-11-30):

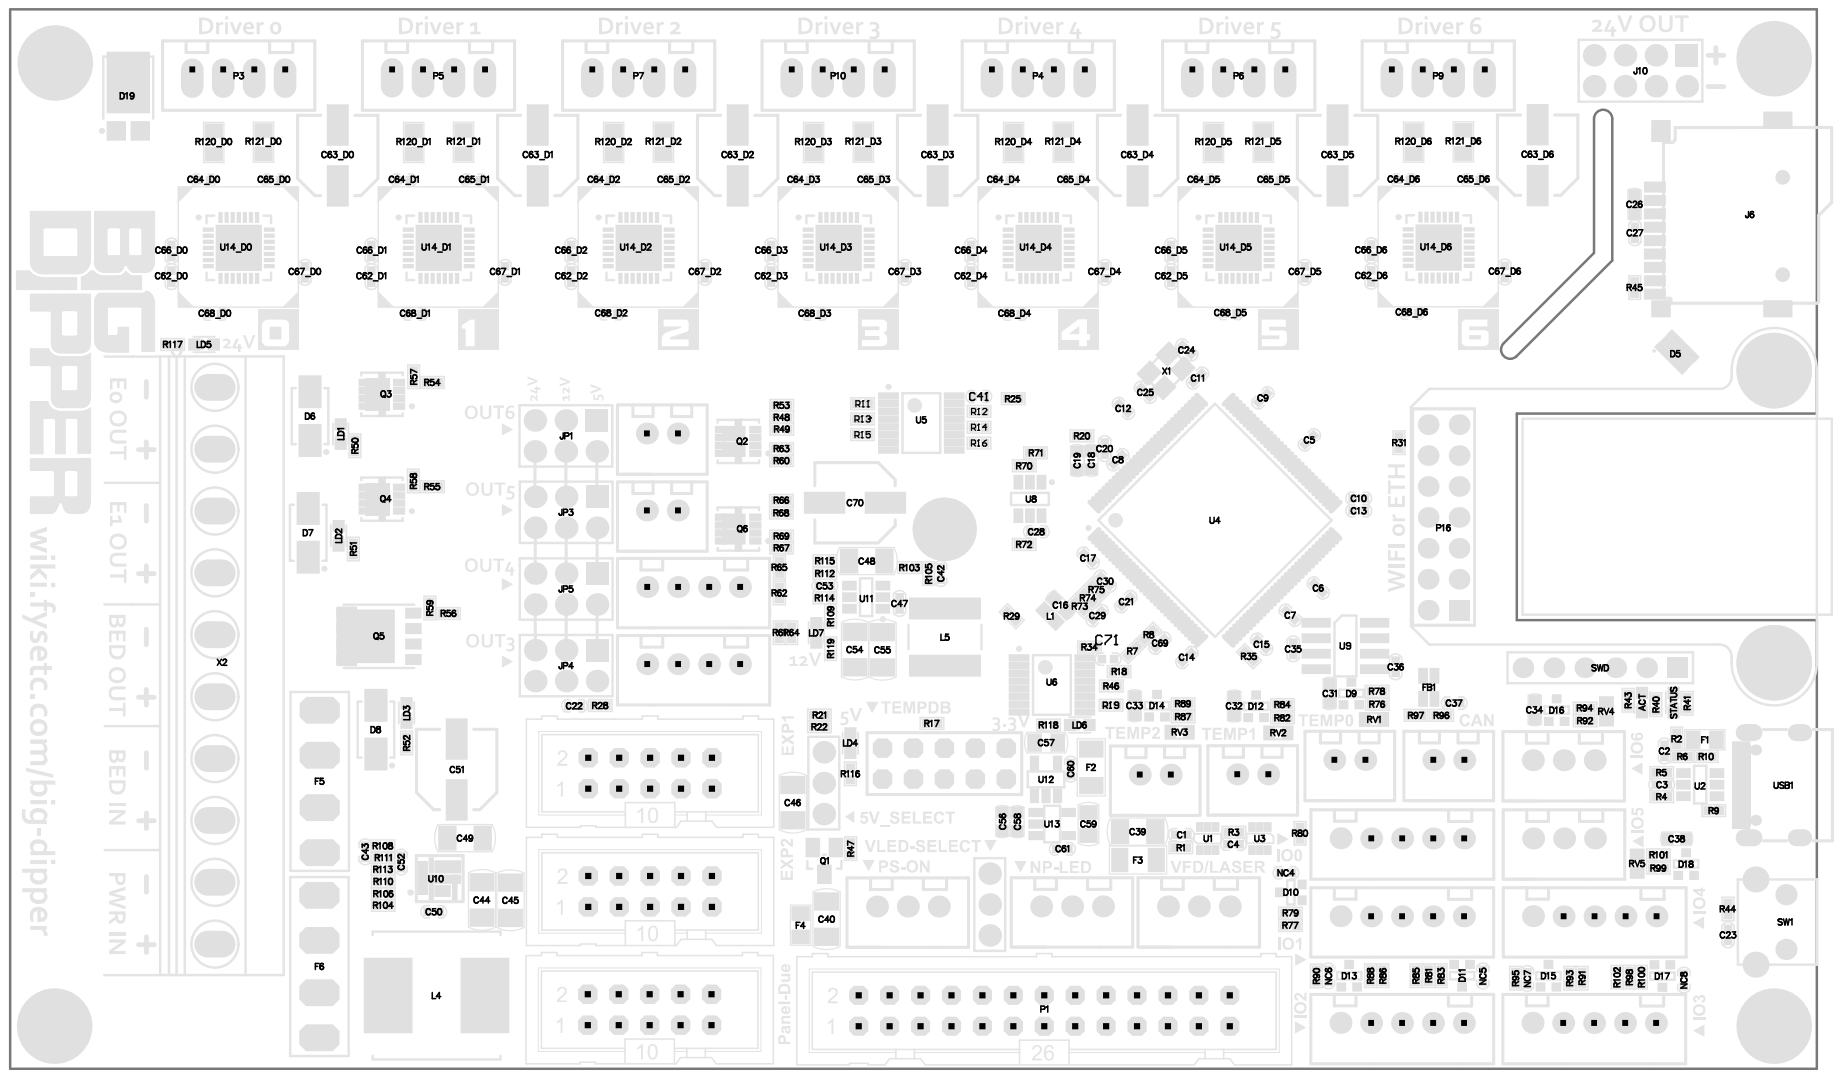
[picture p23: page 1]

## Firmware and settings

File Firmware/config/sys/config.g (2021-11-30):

; Configuration file for Duet 3 Mini 5+ (firmware version 3)
; executed by the firmware on start-up
;
; generated by RepRapFirmware Configuration Tool v3.2.3 on Sat Mar 13 2021 18:31:13 GMT+0800 (中国标准时间)

; General preferences
G90                                             ; send absolute coordinates...
M83                                             ; ...but relative extruder moves
M550 P"big-dipper"                         		; set printer name

; Network
；M552 S1                                         ; enable network
M586 P0 S1                                      ; enable HTTP
M586 P1 S0                                      ; disable FTP
M586 P2 S0                                      ; disable Telnet

; Drives
M569 P0.0 S0                                    ; physical drive 0.0 goes forwards
M569 P0.1 S0                                    ; physical drive 0.1 goes forwards
M569 P0.2 S0                                    ; physical drive 0.1 goes forwards
M569 P0.3 S0                                    ; physical drive 0.2 goes forwards
M569 P0.4 S0                                    ; physical drive 0.3 goes forwards
M569 P0.5 S0                                    ; physical drive 0.4 goes forwards
M569 P0.6 S0                                    ; physical drive 0.5 goes forwards
M584 X0.0 Y0.1 Z0.2 E0.3:0.4:0.5:0.6            ; set drive mapping
M350 X16 Y16 Z16 E16:16:16:16 I1                ; configure microstepping with interpolation
M92 X80 Y80 Z400 E400:400:400:400      			; set steps per mm
M566 X900 Y900 Z60 E600:600:600:600    			; set maximum instantaneous speed changes (mm/min)
M203 X6000 Y6000 Z360 E6000:6000:6000:6000		; set maximum speeds (mm/min)
M201 X500 Y500 Z20 E500:500:500:500    			; set accelerations (mm/s^2)
M906 X800 Y800 Z800 E800:800:800:800 I30        ; set motor currents (mA) and motor idle factor in per cent
M84 S30                                         ; Set idle timeout

; Axis Limits
M208 X0 Y0 Z0 S1                                ; set axis minima
M208 X230 Y210 Z200 S0                          ; set axis maxima

; Endstops
M574 X1 S1 P"io1.in"              				; configure active-high endstop for low end on X via pin io0.in
M574 Y1 S1 P"io2.in"              				; configure active-high endstop for low end on Y via pin io1.in
M574 Z1 S1 P"io3.in"                                    

; Heaters
M308 S0 P"temp0" Y"thermistor" T100000 B4138    ; configure sensor 0 as thermistor on pin temp0
M950 H0 C"out0" T0                              ; create bed heater output on out0 and map it to sensor 0
M307 H0 B1 S1.00                                ; enable bang-bang mode for the bed heater and set PWM limit
M140 H0                                         ; map heated bed to heater 0
M143 H0 S120                                    ; set temperature limit for heater 0 to 120C
M308 S1 P"temp1" Y"thermistor" T100000 B4138    ; configure sensor 1 as thermistor on pin temp1
M950 H1 C"out1" T1                              ; create nozzle heater output on out1 and map it to sensor 1
M307 H1 B0 S1.00                                ; disable bang-bang mode for heater  and set PWM limit
M143 H1 S280                                    ; set temperature limit for heater 1 to 280C
M308 S2 P"temp2" Y"thermistor" T100000 B4138    ; configure sensor 2 as thermistor on pin temp2
M950 H2 C"out2" T2                              ; create nozzle heater output on out2 and map it to sensor 2
M307 H2 B0 S1.00                                ; disable bang-bang mode for heater  and set PWM limit
M143 H2 S280                                    ; set temperature limit for heater 2 to 280C

; tempdb
M308 S3 P"spi.cs1" Y"thermocouple-max31855" K"J";E/K/S/B/T/J/N/R
M950 H3 C"out3.tach" T3
M307 H3 B0 S1.00                                ; disable bang-bang mode for heater  and set PWM limit
M143 H3 S280  
M308 S4 P"spi.cs2" Y"thermocouple-max31855" K"J";E/K/S/B/T/J/N/R	 K"J"
M950 H4 C"out4.tach" T4
M307 H4 B0 S1.00                                ; disable bang-bang mode for heater  and set PWM limit
M143 H4 S280 

; Fans
M950 F0 C"out3" Q500                            ; create fan 0 on pin out3 and set its frequency
M106 P0 S0 H-1                                  ; set fan 0 value. Thermostatic control is turned off
M950 F1 C"out4" Q500                            ; create fan 1 on pin out4 and set its frequency
M106 P1 S0 H-1                                  ; set fan 1 value. Thermostatic control is turned off
M950 F2 C"out5" Q500                            ; create fan 2 on pin out5 and set its frequency
M106 P2 S0 H-1                                  ; set fan 2 value. Thermostatic control is turned off
M950 F3 C"out6" Q500                            ; create fan 3 on pin out6 and set its frequency
M106 P3 S0 H-1                                  ; set fan 3 value. Thermostatic control is turned off

; Tools
M563 P0 D0 H1 F0                              	; define tool 0
G10 P0 X0 Y0 Z0                                 ; set tool 0 axis offsets
G10 P0 R0 S0                                    ; set initial tool 0 active and standby temperatures to 0C
M563 P1 D1 H2 F1                              	; define tool 1
G10 P1 X0 Y0 Z0                                 ; set tool 1 axis offsets
G10 P1 R0 S0                                    ; set initial tool 1 active and standby temperatures to 0C
M563 P2 D2 H3 F2                                ; define tool 2
G10 P2 X0 Y0 Z0                                 ; set tool 2 axis offsets
G10 P2 R0 S0 									; set initial tool 2 active and standby temperatures to 0C
M563 P3 D3 H4 F3                                ; define tool 3
G10 P2 X0 Y0 Z0                                 ; set tool 3 axis offsets
G10 P2 R0 S0 									; set initial tool 3 active and standby temperatures to 0C

; Custom settings are not defined
M918 P2 E2 F2000000 C40 R6                 		; enable ST7567-based 12864 display
M150 X2 R255 U255 B255 S3   					; set all 3 LEDs to white

; Miscellaneous
M575 P1 S1 B57600                               ; enable support for PanelDue
M564 H0 
M302 P1

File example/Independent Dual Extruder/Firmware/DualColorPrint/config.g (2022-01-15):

; Configuration file for Duet 3 Mini 5+ (firmware version 3.3)
; executed by the firmware on start-up
;
; generated by RepRapFirmware Configuration Tool v3.3.10 on Fri Dec 10 2021 21:27:52 GMT+0100 (Mitteleuropäische Normalzeit)

; General preferences
G90                                             ; send absolute coordinates...
M83                                             ; ...but relative extruder moves
M550 P"Weedo X40v2"                             ; set printer name

; Wait a moment for the CAN expansion boards to start
G4 S2

; Network
M551 P"reprap"                                  ; set password
M552 S1                                         ; enable network
M586 P0 S1                                      ; enable HTTP
M586 P1 S0                                      ; disable FTP
M586 P2 S0                                      ; disable Telnet

; Drives
M569 P0.0 S0 V50                                    ; Y Axis physical drive 0.0 goes backwards V50 to leave spreadCycle Mode
M569 P0.1 S0 V50                                    ; Z left Axis physical drive 0.1 goes backwards 
M569 P0.2 S0 V50                                    ; Z right Axis physical drive 0.2 goes backwards 
M569 P0.3 S1 V50                                    ; X left Axis physical drive 0.3 goes forwards 
M569 P0.4 S0 V50                                    ; X right Axis physical drive 0.4 goes backwards 
M569 P0.5 S1 V50                                    ; E left Axis physical drive 0.5 goes forwards 
M569 P0.6 S1 V50                                    ; E right Axis physical drive 0.6 goes forwards 
M584 X0.3 Y0.0 Z0.1:0.2 U0.4 E0.5:0.6           ; set drive mapping, Driver number for additional axes U for second X
M350 X16 Y16 Z16:16 U16 E16:16 I1                      ; configure microstepping with interpolation
M92 X94.14 Y94.14 Z400.00:400.00 U94.14 E94.90:94.90        ; set steps per mm
M566 X900.00 Y900.00 Z80.00:80.00 U900.00 E120.00:120.00      ; set maximum instantaneous speed changes (mm/min)
M203 X16000.00 Y16000.00 Z500.00:500.00 U16000.00 E1200.00:1200.00 ; set maximum speeds (mm/min)
M201 X1000.00 Y1000.00 Z20.00:20.00 U1000.00 E250.00:250.00      ; set accelerations (mm/s^2)
M906 X700 Y700 Z700:700 U700 E500:500 I30                ; set motor currents (mA) and motor idle factor in per cent
M84 S30                                         ; Set idle timeout

; Axis Limits
M208 X-51.80 U0 Y-11 Z0:0 S1                                ; set axis minima, X-51.8 for the Extruder to go negative into park position, S1 = set axis minimum
M208 X300.00 U351.80 Y305 Z400:400 S0                          ; set axis maxima, U351.8 for the Extruder to go out of bed into park position, S0 = set axis maximum

; Endstops
M574 X1 S1 P"!io6.in"                            ; configure switch-type (e.g. microswitch) endstop for low end on X via pin io6.in
M574 U2 S1 P"!io4.in"                            ; configure switch-type (e.g. microswitch) endstop for high end on U via pin io4.in
M574 Y1 S1 P"!io5.in"                            ; configure switch-type (e.g. microswitch) endstop for low end on Y via pin io5.in
M574 Z1 S2                                      ; configure Z-probe endstop for low end on Z

; Z-Probe
M558 P5 C"!io0.in" H5 F240 T10000               ; set Z probe type to unmodulated and the dive height + speeds for Probing and Travel
G31 P500 X-35 Y0 Z1.030                           ; set Z probe trigger value, offset and trigger height
M557 X10:290 Y10:290 S50                        ; set Mesh bed size

; Heaters
M308 S0 P"temp2" Y"thermistor" T100000 B4092    ; configure sensor 0 as thermistor on pin temp2
M950 H0 C"out0" T0                              ; create bed heater output on out0 and map it to sensor 0
M307 H0 B0 R0.317 C372.9 D3.16 S1.00 V24.1      ; disable bang-bang mode for the bed heater and set PWM limit with PID tune
M140 H0                                         ; map heated bed to heater 0
M143 H0 S100                                    ; set temperature limit for heater 0 to 100C
M308 S1 P"temp0" Y"thermistor" T100000 B4092    ; configure sensor 1 as thermistor on pin temp0
M950 H1 C"out1" T1                              ; create nozzle heater output on out1 and map it to sensor 1
M307 H1 B0 R3.302 C205.8 D7.27 S1.00 V24.1      ; disable bang-bang mode for the bed heater and set PWM limit with PID tune
M143 H1 S260                                    ; set temperature limit for heater 1 to 260C
M308 S2 P"temp1" Y"thermistor" T100000 B4092    ; configure sensor 2 as thermistor on pin temp1
M950 H2 C"out2" T2                              ; create nozzle heater output on out2 and map it to sensor 2
M307 H2 B0 R3.528 C210.1 D7.19 S1.00 V24.1      ; disable bang-bang mode for the bed heater and set PWM limit with PID tune
M143 H2 S260                                    ; set temperature limit for heater 2 to 260C

; Fans
M950 F0 C"out6" Q500                            ; create fan 0 on pin out6 and set its frequency
M106 P0 C"Fan0 E0" S1 H1 T45                    ; set fan 0 name and value. Thermostatic control is turned on
M950 F1 C"out5" Q500                            ; create fan 1 on pin out5 and set its frequency
M106 P1 C"Fan0 E1" S1 H2 T45                    ; set fan 1 name and value. Thermostatic control is turned on
M950 F2 C"out4" Q500                            ; create fan 2 on pin out4 and set its frequency
M106 P2 C"Part E0" S0 I0 H-1                    ; set fan 2 name and value. Thermostatic control is turned off
M950 F3 C"out3" Q500                            ; create fan 3 on pin out3 and set its frequency
M106 P3 C"Part E1" S0 I0 H-1                    ; set fan 3 name and value. Thermostatic control is turned off

; Tools
M563 P0 S"Nozzle left" D0 H1 F2                 ; define tool 0
G10 P0 X0 Y0 Z0                                 ; set tool 0 axis offsets
G10 P0 R0 S0                                    ; set initial tool 0 active and standby temperatures to 0C
M572 D0 S1.1                                    ; Preasure Advanced Seetings for Tool 0
M563 P1 S"Nozzle right" D1 H2 X3 F3             ; define tool 1, X3 tells the firmware that the X axis should be mapped to axis #3 which is the U axis.
G10 P1 Y0 U-3.4 Z0                            ; set tool 1 axis offsets
G10 P1 R0 S0                                    ; set initial tool 1 active and standby temperatures to 0C
M572 D1 S1.1                                    ; Preasure Advanced Seetings for Tool 1

; Custom settings are not defined

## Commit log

2021-11-30 Upload firmware and hardware files
    [bed.g, cancel.g, config.g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]
2021-12-06 Upload CAD file
2021-12-06 add 3D files
    [BIG-DIPPER V1.1.dwg]
2021-12-12 Add files via upload
    Transfer from frok into branch
    [FYSETC Big Dipper v1.1.stl]
2021-12-21 Add files via upload
    Tested Version. But not a realese.
    [bed.g, config.g, homeall.g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]
2021-12-21 Add Preasure Advanced
    [config.g]
2022-02-11 Rename example/resources/readme.md to example/Independent Dual Extruder (IDEX)/resources/readme.md
2022-02-11 Rename example/Firmware/DualColorPrint/readme.md to example/Independent Dual Extruder (IDEX)/FirmwareDualColorPrint/readme.md
2022-02-11 Rename example/Firmware/DualColorPrint/bed.g to example/Independent Dual Extruder (IDEX)/Firmware/DualColorPrint/bed.g
    [bed.g]
2022-02-11 Rename example/Firmware/DualColorPrint/config.g to example/Independent Dual Extruder (IDEX)/Firmware/DualColorPrint/config.g
    [config.g]
2022-02-11 Rename example/Firmware/DualColorPrint/homeall.g to example/Independent Dual Extruder (IDEX)/Firmware/DualColorPrint/homeall.g
    [homeall.g]
2022-02-11 Rename example/Firmware/DualColorPrint/homeu.g to example/Independent Dual Extruder (IDEX)/Firmware/DualColorPrint/homeu.g
    [homeu.g]
2022-02-11 Rename example/Firmware/DualColorPrint/homex.g to example/Independent Dual Extruder (IDEX)/Firmware/DualColorPrint/homex.g
    [homex.g]
2022-02-11 Rename example/Firmware/DualColorPrint/homey.g to example/Independent Dual Extruder (IDEX)/Firmware/DualColorPrint/homey.g
    [homey.g]
2022-02-11 Rename example/Firmware/DualColorPrint/homez.g to example/Independent Dual Extruder (IDEX)/Firmware/DualColorPrint/homez.g
    [homez.g]
2022-02-11 Rename example/Firmware/DualColorPrint/pause.g to example/Independent Dual Extruder (IDEX)/Firmware/DualColorPrint/pause.g
    [pause.g]
2022-02-11 Rename example/Firmware/DualColorPrint/resume.g to example/Independent Dual Extruder (IDEX)/Firmware/DualColorPrint/resume.g
    [resume.g]
2022-02-11 Rename example/Firmware/DualColorPrint/resurrect.g to example/Independent Dual Extruder (IDEX)/Firmware/DualColorPrint/resurrect.g
    [resurrect.g]
2022-02-11 Rename example/Firmware/DualColorPrint/sleep.g to example/Independent Dual Extruder (IDEX)/Firmware/DualColorPrint/sleep.g
    [sleep.g]
2022-02-11 Rename example/Firmware/DualColorPrint/stop.g to example/Independent Dual Extruder (IDEX)/Firmware/DualColorPrint/stop.g
    [stop.g]
2022-02-11 Rename example/Firmware/DualColorPrint/tfree0.g to example/Independent Dual Extruder (IDEX)/Firmware/DualColorPrint/tfree0.g
    [tfree0.g]
2022-02-11 Rename example/Firmware/DualColorPrint/tfree1.g to example/Independent Dual Extruder (IDEX)/Firmware/DualColorPrint/tfree1.g
    [tfree1.g]
2022-02-11 Rename example/Firmware/DualColorPrint/tpost0.g to example/Independent Dual Extruder (IDEX)/Firmware/DualColorPrint/tpost0.g
    [tpost0.g]
2022-02-11 Rename example/Firmware/DualColorPrint/tpost1.g to example/Independent Dual Extruder (IDEX)/Firmware/DualColorPrint/tpost1.g
    [tpost1.g]
2022-02-11 Rename example/Firmware/DualColorPrint/tpre0.g to example/Independent Dual Extruder (IDEX)/Firmware/DualColorPrint/tpre0.g
    [tpre0.g]
2022-02-11 Rename example/Firmware/DualColorPrint/tpre1.g to example/Independent Dual Extruder (IDEX)/Firmware/DualColorPrint/tpre1.g
    [tpre1.g]
2022-02-11 Rename example/Firmware/PrusaSlicerConfig/Weedo X40 Dual Color RRF config.ini to example/Independent Dual Extruder (IDEX)/Firmware/PrusaSlicerConfig/Weedo X40 Dual Color RRF config.ini
2022-02-11 Rename example/Firmware/PrusaSlicerConfig/readme.md to example/Independent Dual Extruder (IDEX)/Firmware/PrusaSlicerConfig/readme.md
2022-02-11 Rename example/Firmware/readme.md to example/Independent Dual Extruder (IDEX)/Firmware/readme.md
2022-02-11 Rename example/readme.md to example/Independent Dual Extruder (IDEX)/readme.md
2022-02-11 Rename example/pictures/readme.md to example/Independent Dual Extruder (IDEX)/pictures/readme.md
2022-02-13 Fixed () in Folder name
    [bed.g, config.g, homeall.g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]
